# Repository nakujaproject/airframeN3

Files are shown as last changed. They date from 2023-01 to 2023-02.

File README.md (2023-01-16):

# airframeN3

This is the repository for the airframe sub-group relating to N3 rocket.

   

## Onboarding

For new members, please check out onboard document [here](Onboarding/newEmployee.md)

## Research

For visitors, check out our research done by members of the airframe team [here](Research/)

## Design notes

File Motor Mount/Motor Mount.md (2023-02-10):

# **MOTOR MOUNTS**

A mount is required to secure the motor in place during flight. 
Requirements for the motor mount are:

	- It should locate the motor within the skin tube of the airframe.
	- It should handle the forces due to the thrust produced by the motor.

The motor mount is located between the motor and the outer skin of the rocket tube. It's dimensions must,
therefore, be known early on in the design phase for better fitment. Since a solid rocket motor is being used for this
project, the proposed motor mount is to consist of a mounting tube and centering rings/bulkheads for ensuring
concentricity and locating the mounting tube in the airframe tube. 

The inner diameter of the mounting tube is dictated by the outer diameter of the rocket motor. The outer diameter of 
mounting tube determines the inner diameter of the bulkheads. The bulkheads are to be made of aluminum or polycarbonate.
Depending on the desired arrangement we can have two main configurations for the motor mount:

	1. Mounting tube integral with the retaining bulkhead.
		- THe mounting tube and retaining bulkhead are machined from one piece of metal. THe only additional 
		  component required is the locationg ring at the other end of the mounting tube. 
		- This enables for quick locating and assembly of the motor mount.
		- Reduces the number of bulkheads to be used.
		- Machining the mounting tube may be difficult.
	Motor mount configuration 1

	2. Mounting tube separate from bulkheads. 
		- This system used a mounting tube and several bulkheads arranged throughout the length of the motor bay
		  for locating and securign the tube in place.
		- Requires several bulkheads.
		- Longer assembly time.
	Motor mount configuration 2

The decision on the mounting configuration will depend on the size of motor selected i.e. thrust and weight since the
mount is supposed to hold the motor in place on application of full thrust.

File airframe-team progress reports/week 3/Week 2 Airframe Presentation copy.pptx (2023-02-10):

## NAKUJA PROJECT WEEK 2 PRESENTATION

AIRFRAME
1ST FEBRUARY 2023

## Past week’s objectives

Preliminary research on the following listed topics:
- Research on the material to fabricate the airframe.
- Feasibility of Aluminum in fabrication of the airframe.
- Research on the material to be used for fabrication. Settled for Aluminium grade 6061.
- Dual parachute deployment
- Research on launchpad and launch lug designs.

## Design examples

- Fully assembled airframe with nose cone, body tube and tail.

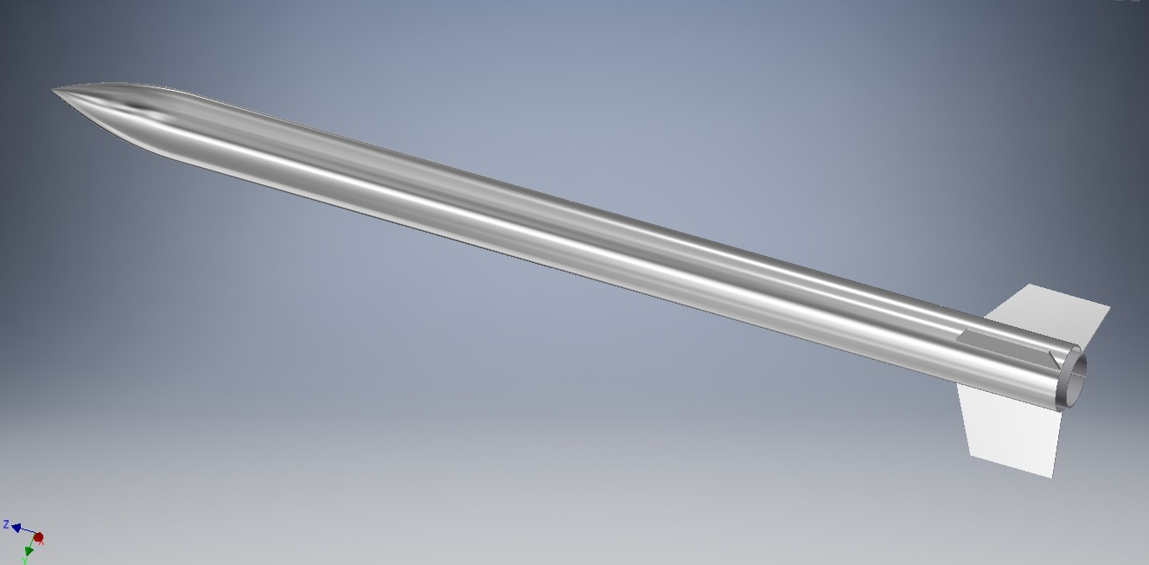
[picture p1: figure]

## Design examples

- Exploded view of the airframe with nose cone, body tube and tail.

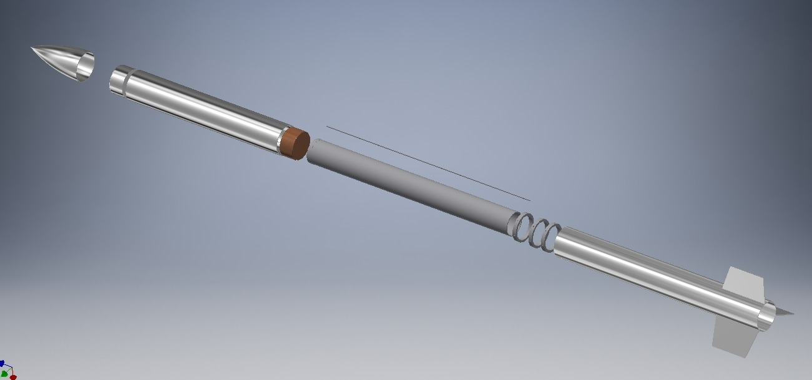
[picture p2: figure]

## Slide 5

- Avionics bay assembly. - Avionics bay inside body tube

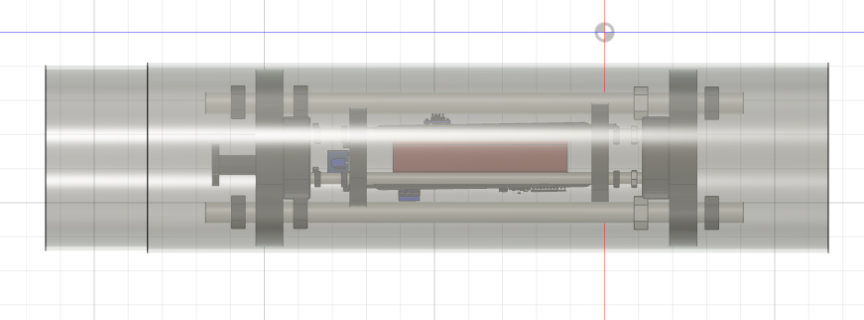
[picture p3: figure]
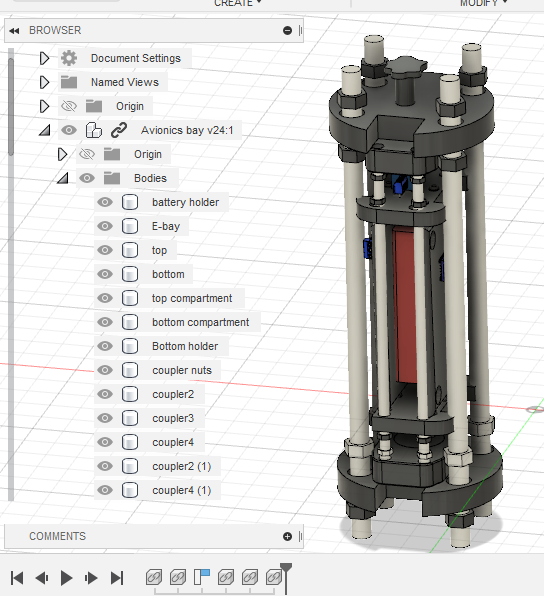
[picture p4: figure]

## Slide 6

- Exploded and assembled view of the motor mount.

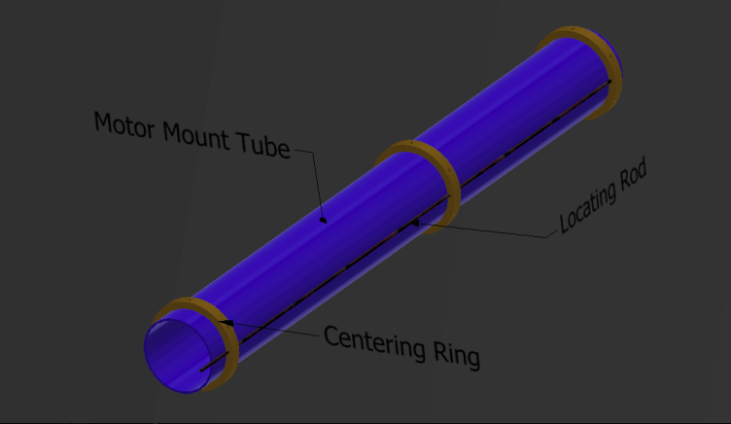
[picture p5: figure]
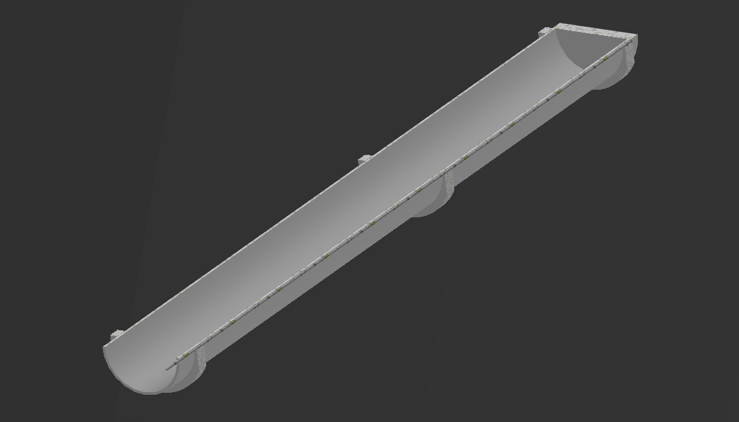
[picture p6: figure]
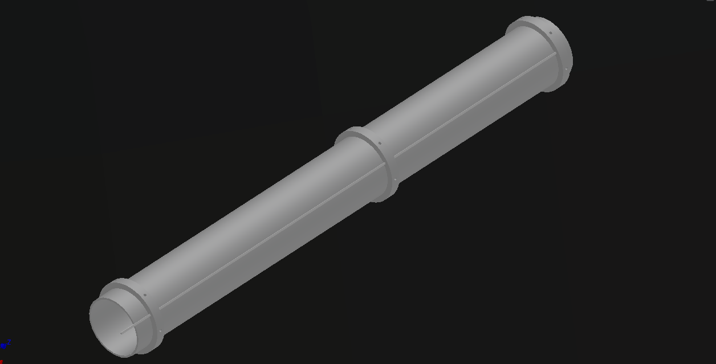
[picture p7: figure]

## Assembled design of the launch pad and launch rod

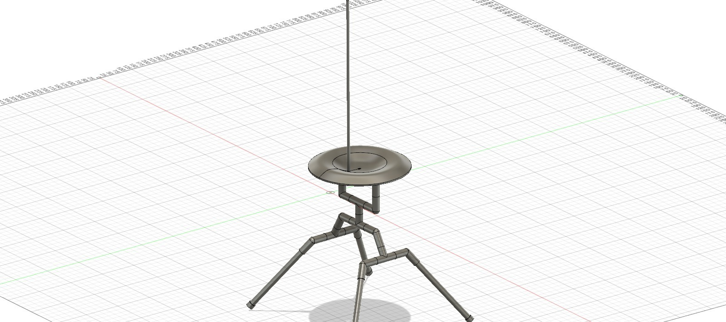
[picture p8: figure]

## Tasklist Spreadsheet

- Link to our Excell tasklist:
https://docs.google.com/spreadsheets/d/1M_BzmsQo8DNNqcfr_GzHXy1NbRIfWbWbaoDP3lDmqlY/edit#gid=1232676584
- Link to Comprehensive Gantt Chart:
Airframe ProjectSchedule (sharepoint.com) (https://studentsjkuatacke-my.sharepoint.com/:x:/r/personal/namuye_innocent_students_jkuat_ac_ke/_layouts/15/Doc.aspx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)
- Link to simplified Gantt Chart:
Simplified Airframe Gantt Chart.xlsx (sharepoint.com) (https://studentsjkuatacke-my.sharepoint.com/:x:/r/personal/namuye_innocent_students_jkuat_ac_ke/_layouts/15/Doc.aspx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)

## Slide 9

- Simplified Airframe Gantt chart

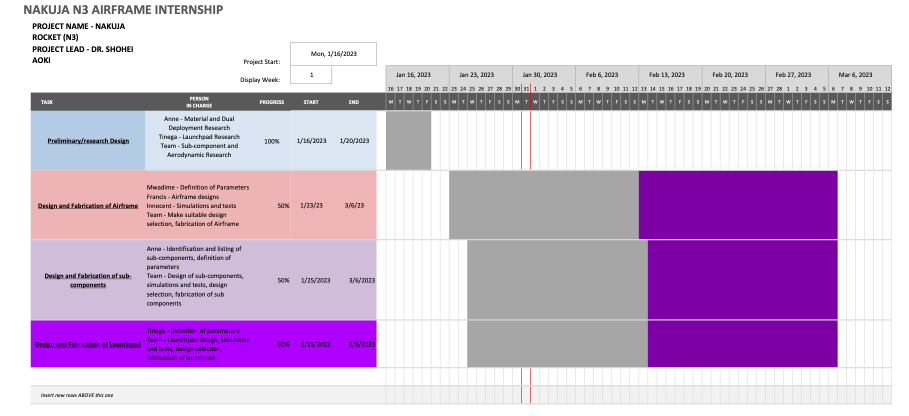
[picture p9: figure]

## Way forward

- Fabricate 5 airframe prototypes
: 3 with fibreglass
; 2 with Aluminium
- One of the fins will be fabricated using carbon fibre
- We are planning to use the aluminum rod instead of sheet for accuracy and ease of fabrication.

## This week’s objectives

- Research and selection of fabrication techniques
- Settle on parameter selection
- Generation of bill of materials
- Finalise on designs
- Make design selection

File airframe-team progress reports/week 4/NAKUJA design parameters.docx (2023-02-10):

Applied Compressive Load

Calculations for the maximum compressive load the rocket can handle given its dimensions are as follows:

Applied Compressive Strength, F_c =(P_(max))/(πDt)

Where, P_(max) is the maximum load on the rocket tube

D is the rocket diameter

t is thickness of the rocket tube

F_c =Compressive strength of aluminium 6061 (120Mpa)

P_(max) =F_c ×π×D×t=120×π×80×2=60,318.578N≅60kN

The actual applied load: (calculated at max Q)

Drag force, F_D =1/2×ρ×C_d ×v^2 ×A

F_D =1/2×1.225×0.64×342^2 ×0.007056=323.52≅325N

Inertia Force, F_(inertia) =ma=10×37=370N

Total applied load=F_D +F_(inertia) =325+370=695N≅700N

The load applied is less than the maximum load the rocket tube can handle. The rocket is thus safe from compression loads during flight.

Maximum Buckling Loads (that the airframe can handle)

Buckling Loads=(γ2πEt^2 cos^2 α)/(√(3(1-μ^2 )))

Where α is the conical semi-angle.

γ=0.33

Buckling loads=(0.33×2π×69×10^9 ×0.003^2 ×cos^2 9.46)/(√(3(1-0.33^2 )))=766.235kN≅770kN

Coefficient of drag on Nose and Body Tube

C_(D_N) +C_(D_(BT)) =1.02C_F (1+1.5/((L/d)^2))(S_(BT))/(A_(BT))

C_(D_N) +C_(D_(BT)) =1.02×2.387×10^(-3) (1+1.5/((186/84)^2))0.40715/0.402124

C_(D_N) +C_(D_(BT)) =2.43474×10^(-3) ×1.3059×1.0125=3.2193×10^(-3)

Base Drag Coefficient

C_(D_B) =0.029/(√(C_(D_N) +C_(D_(BT))))=0.029/(√(3.2193×10^(-3)))=0.51112

Fin Drag Coefficient

C_(D_F) =2C_F (1+2t/(C_(ave)))(S_F)/(A_(BT))=2×2.387^(-3) (1+20.003/0.115)0.0095/0.402124=1.1867×10^(-4)

Intermediate Drag Coefficient

C_(D_I) =C_F (1+2t/(C_(ave)))(C_R)/(S_(BT))∙dn=2.387×10^(-3) (1+20.003/0.115)0.08/0.40715∙0.08×3

C_(D_I) =1.18437×10^(-4)

Total Drag Coefficient

C_D =C_(D_N) +C_(D_(BT)) +C_(D_B) +C_(D_F) +C_(D_I) =3.2193×10^(-3) +0.51112+1.1867×10^(-4) +1.18437×10^(-4) ≅0.5146

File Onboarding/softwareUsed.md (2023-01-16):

# Used software

## Initial Design

Currently we are using [Openrocket v22.02](https://openrocket.info/downloads.html?vers=22.02.beta.05)

## Computer Aided Design

Currently we are using [Inventor 2022](https://knowledge.autodesk.com/support/inventor/learn-explore/caas/CloudHelp/cloudhelp/2020/ENU/Inventor-WhatsNew/files/GUID-8126E8EE-422A-4DEF-9B14-513D87BD4122-htm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's,the%20release%20of%20Inventor%202020.&text=Inventor%202020%20delivers%3A,a%20modernized%20look%20and%20feel.)

## Analysis

For fluid analysis we are using [CFD 2022](https://knowledge.autodesk.com/support/cfd/troubleshooting/caas/downloads/content/autodesk-cfd-2019-download-and-install-help-documentation.html)

The Autodesk fusion version we are using is [Fusion 360](https://www.autodesk.com/products/fusion-360/free-trial)

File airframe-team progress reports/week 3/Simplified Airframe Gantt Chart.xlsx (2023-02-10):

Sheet: About
SIMPLE GANTT CHART by Vertex42.com (https://www.vertex42.com/ExcelTemplates/simple-gantt-chart.html)
https://www.vertex42.com/ExcelTemplates/simple-gantt-chart.html
About This Template
This template provides a simple way to create a Gantt chart to help visualize and track your project. Simply enter your tasks and start and end dates - no formulas required. The bars in the Gantt chart represent the duration of the task and are displayed using conditional formatting. Insert new tasks by inserting new rows.
Guide for Screen Readers
There are 2 worksheets in this workbook. TimeSheet About The instructions for each worksheet are in the A column starting in cell A1 of each worksheet. They are written with hidden text. Each step guides you through the information in that row. Each subsequent step continues in cell A2, A3, and so on, unless otherwise explicitly directed. For example, instruction text might say "continue to cell A6" for the next step. This hidden text will not print. To remove these instructions from the worksheet, simply delete column A.
Additional Help
Click on the link below to visit vertex42.com and learn more about how to use this template, such as how to calculate days and work days, create task dependencies, change the colors of the bars, add a scroll bar to make it easier to change the display week, extend the date range displayed in the chart, etc.
How to Use the Simple Gantt Chart (https://www.vertex42.com/ExcelTemplates/simple-gantt-chart.html)
More Project Management Templates
Visit Vertex42.com to download other project management templates, including different types of project schedules, Gantt charts, tasks lists, etc.
Project Management Templates (https://www.vertex42.com/ExcelTemplates/excel-project-management.html)
About Vertex42
Vertex42.com provides over 300 professionally designed spreadsheet templates for business, home, and education - most of which are free to download. Their collection includes a variety of calendars, planners, and schedules as well as personal finance spreadsheets for budgeting, debt reduction, and loan amortization.
Businesses will find invoices, time sheets, inventory trackers, financial statements, and project planning templates. Teachers and students will find resources such as class schedules, grade books, and attendance sheets. Organize your family life with meal planners, checklists, and exercise logs. Each template is thoroughly researched, refined, and improved over time through feedback from thousands of users.

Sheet: ProjectSchedule
NAKUJA N3 AIRFRAME INTERNSHIP
Enter Company Name in cell B2. | PROJECT NAME - NAKUJA ROCKET (N3)
Enter the name of the Project Lead in cell B3. Enter the Project Start date in cell E3. Project Start: label is in cell C3. | PROJECT LEAD - DR. SHOHEI AOKI | Project Start: |  | 2023-01-16
The Display Week in cell E4 represents the starting week to display in the project schedule in cell I4. The project start date is considered Week 1. To change the display week, simply enter a new week number in cell E4. The starting date for each week, starting with the display week from cell E4, starts in cell I4 and is auto calculated. There are 8 weeks represented in this view from cell I4 through cell BF4. You should not modify these cells. Display Week: label is in cell C4. |  | Display Week: |  | 1 |  | 2023-01-16 |  |  |  |  |  |  | 2023-01-23 |  |  |  |  |  |  | 2023-01-30 |  |  |  |  |  |  | 2023-02-06 |  |  |  |  |  |  | 2023-02-13 |  |  |  |  |  |  | 2023-02-20 |  |  |  |  |  |  | 2023-02-27 |  |  |  |  |  |  | 2023-03-06
Cells I5 through BL5 contain the day number for the week represented in the cell block above each date cell and are auto calculated. You should not modify these cells. Today's date is outlined in Red (hex #AD3815) from today's date in row 5 through the entire date column to the end of the project schedule. |  |  |  |  |  | 2023-01-16 | 2023-01-17 | 2023-01-18 | 2023-01-19 | 2023-01-20 | 2023-01-21 | 2023-01-22 | 2023-01-23 | 2023-01-24 | 2023-01-25 | 2023-01-26 | 2023-01-27 | 2023-01-28 | 2023-01-29 | 2023-01-30 | 2023-01-31 | 2023-02-01 | 2023-02-02 | 2023-02-03 | 2023-02-04 | 2023-02-05 | 2023-02-06 | 2023-02-07 | 2023-02-08 | 2023-02-09 | 2023-02-10 | 2023-02-11 | 2023-02-12 | 2023-02-13 | 2023-02-14 | 2023-02-15 | 2023-02-16 | 2023-02-17 | 2023-02-18 | 2023-02-19 | 2023-02-20 | 2023-02-21 | 2023-02-22 | 2023-02-23 | 2023-02-24 | 2023-02-25 | 2023-02-26 | 2023-02-27 | 2023-02-28 | 2023-03-01 | 2023-03-02 | 2023-03-03 | 2023-03-04 | 2023-03-05 | 2023-03-06 | 2023-03-07 | 2023-03-08
This row contains headers for the project schedule that follows below them. Navigate from B6 through BL 6 to hear the content. The first letter of each day of the week for the date above that heading, starts in cell I6 and continues through cell BL6. All project timeline charting is auto generated based on the start and end dates entered, using conditional formats. Do not modify content in cells within columns after column I starting with cell I7. | TASK | PERSON IN CHARGE | PROGRESS | START | END | M | T | W | T | F | S | S | M | T | W | T | F | S | S | M | T | W | T | F | S | S | M | T | W | T | F | S | S | M | T | W | T | F | S | S | M | T | W | T | F | S | S | M | T | W | T | F | S | S | M | T | W
Cell B8 contains the Phase 1 sample title. Enter a new Title in cell B8. Enter a name to assign the phase to, if it applies for your project, in cell C8. Enter Progress for the entire phase, if it applies for your project, in cell D8. Enter the start and end dates for the entire phase, if it applies for your project, in cells E8 and F8. The Gantt chart will automatically fill in the appropriate dates and shade according to the progress entered. To delete the phase and work only from tasks, simply delete this row. | Preliminary/research Design | Anne - Material and Dual Deployment Research Tinega - Launchpad Research Team - Sub-component and Aerodynamic Research | 100% | 2023-01-16 | 2023-01-20
The cell at right contains the Phase 2 sample title. You can create a new phase at any time within column B. This project schedule does not require phases. To remove the phase, simply delete the row. To create a new phase block in this row, enter a new Title in cell at right. To continue adding tasks to the phase above, enter a new row above this one and fill in the task data as in cell A9's instruction. Update the Phase details in cell at right based on cell A8's instruction. Continue navigating down column A cells to learn more. If you haven't added any new rows in this worksheet, you will find 2 additional sample phase blocks have been created for you in cells B20 and B26. Otherwise, navigate through column A cells to find the additional blocks. Repeat the instructions from cells A8 and A9 whenever you need to. | Design and Fabrication of Airframe | Mwadime - Definition of Parameters Francis - Airframe designs Innocent - Simulations and tests Team - Make suitable design selection, fabrication of Airframe | 50% | 2023-01-23 | 2023-03-06
Sample phase title block | Design and Fabrication of sub-components | Anne - Identification and listing of sub-components, definition of parameters Team - Design of sub-components, simulations and tests, design selection, fabrication of sub components | 50% | 2023-01-25 | 2023-03-06
 | Design and Fabrication of Launchpad | Tinega - Definition of parameters Team - Launchpad design, simulation and tests, design selection, fabrication of launchpad | 50% | 2023-01-25 | 2023-03-06
This is an empty row
This row marks the end of the Project Schedule. DO NOT enter anything in this row. Insert new rows ABOVE this one to continue building out your Project Schedule. | Insert new rows ABOVE this one
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

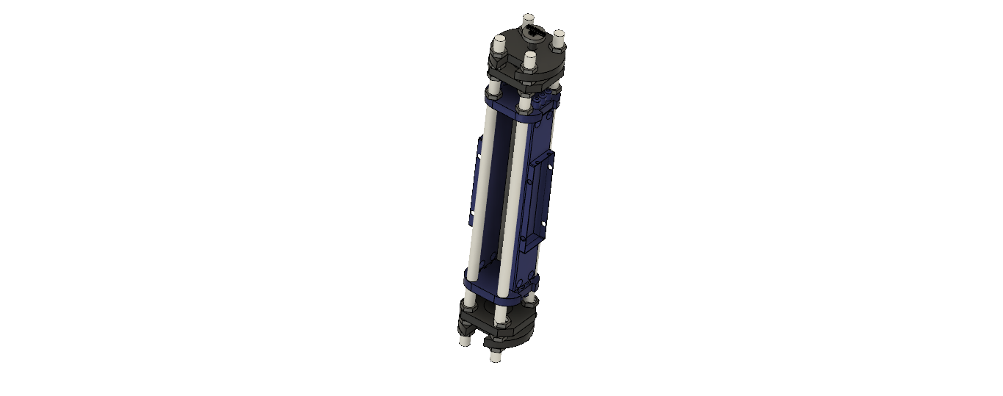
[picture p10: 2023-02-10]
airframe-team progress reports/week 4/Airframe Design Images/N3 avionics bay.png

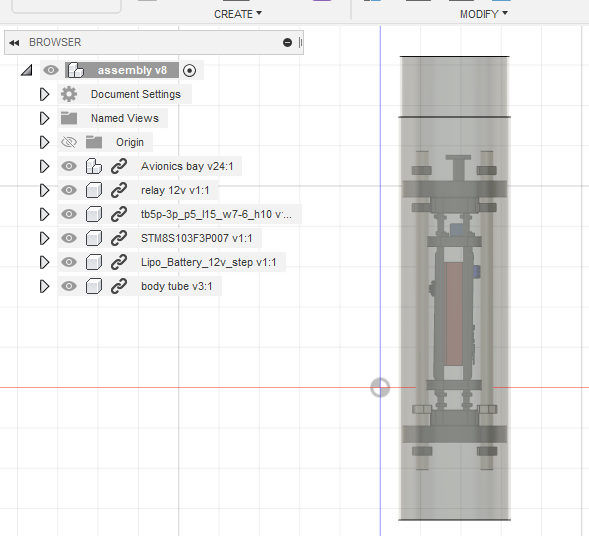
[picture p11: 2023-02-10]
airframe-team progress reports/week 3/Avionics bayV1/vionics .png

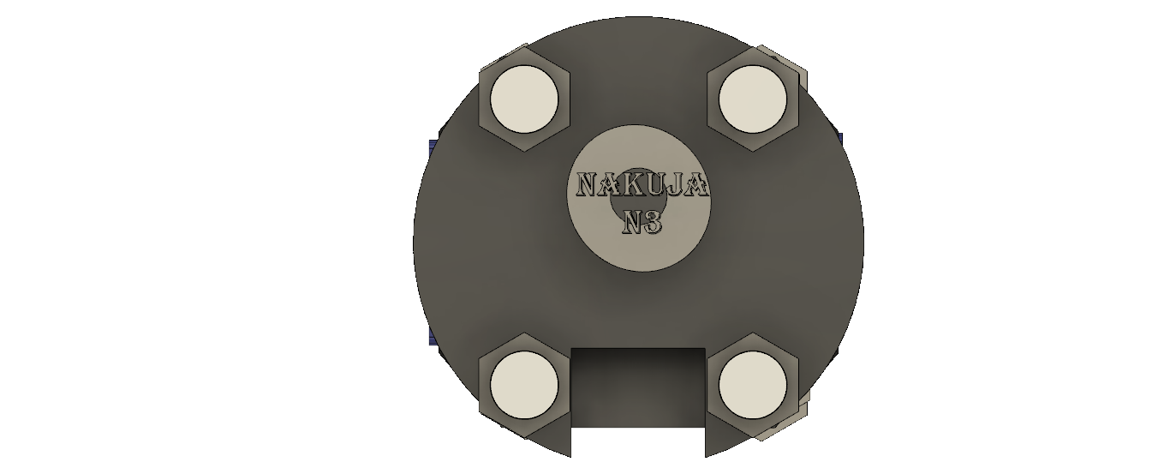
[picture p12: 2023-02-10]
airframe-team progress reports/week 4/Airframe Design Images/Top view.png

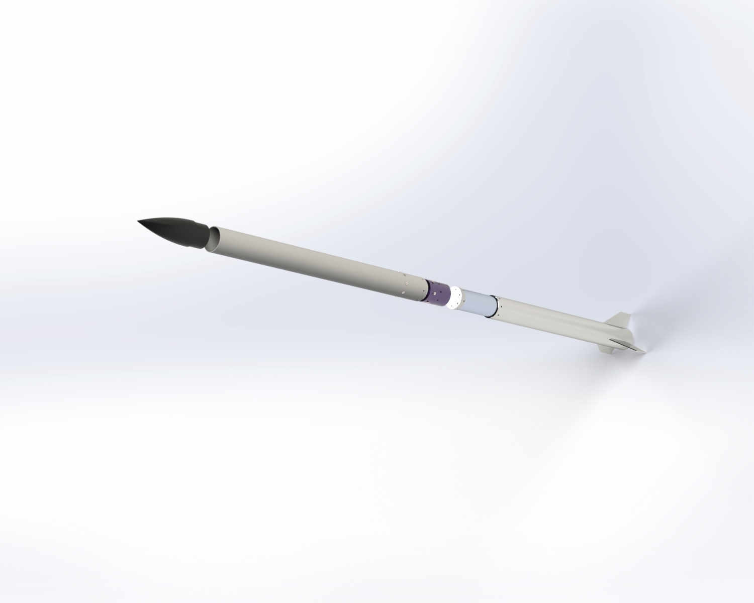
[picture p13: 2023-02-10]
airframe-team progress reports/week 4/Airframe Design Images/Rendered View.jpeg

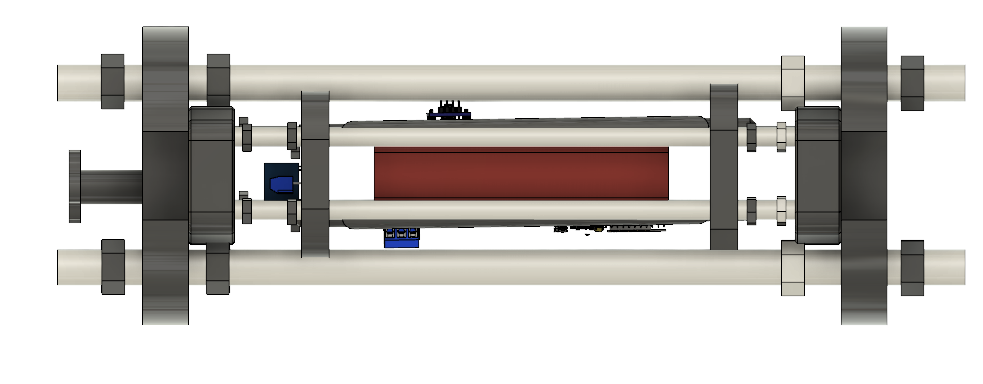
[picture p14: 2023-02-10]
airframe-team progress reports/week 3/Avionics bayV1/frontview.png

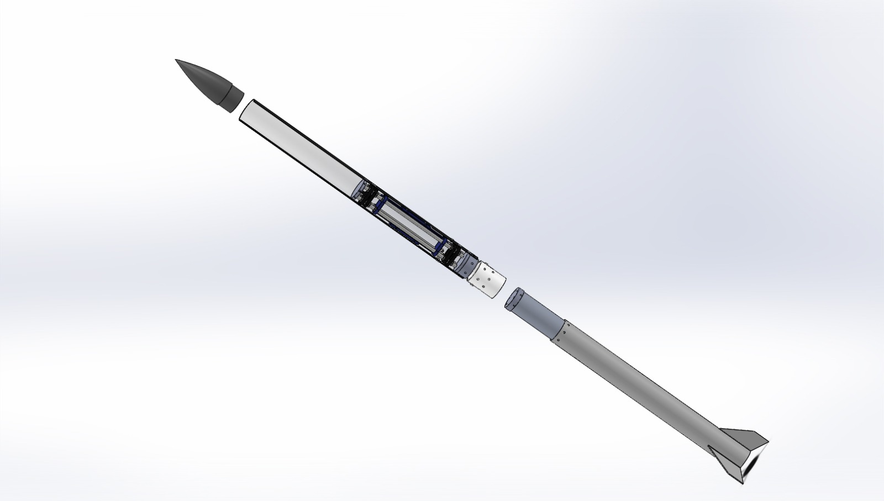
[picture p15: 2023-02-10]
airframe-team progress reports/week 4/Airframe Design Images/Exploaded view.jpeg

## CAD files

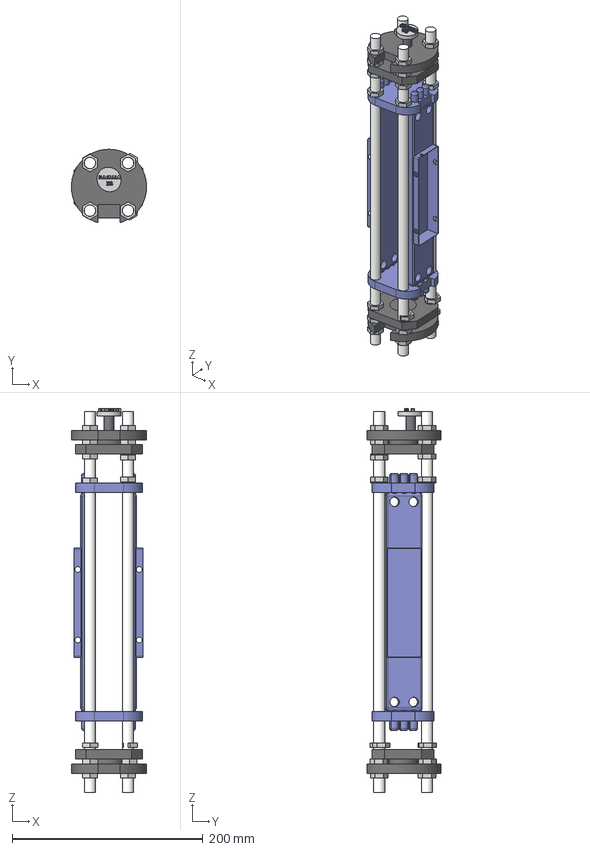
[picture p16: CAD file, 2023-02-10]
airframe-team progress reports/week 4/CAD files/Final assemblyv2 v9.step
79.0 x 77.3 x 403.0 mm
Holder Avionics Bay
holder_rod x 4
Holder Avionics Bay v5(Mirror)
bottom compartment
Bottom coupler
bottom compartment v11(Mirror)
Bottom coupler v4(Mirror)
Ebay x 2
Holder
holder_nut x 28

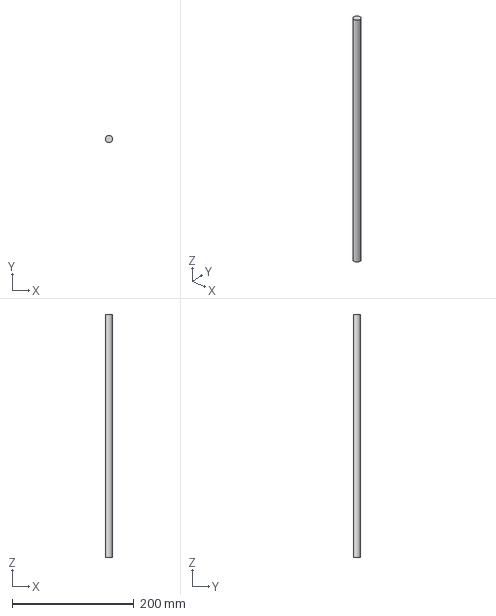
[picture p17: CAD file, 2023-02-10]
airframe-team progress reports/week 4/CAD files/N3 holder_rod .step
11.8 x 11.8 x 400.0 mm

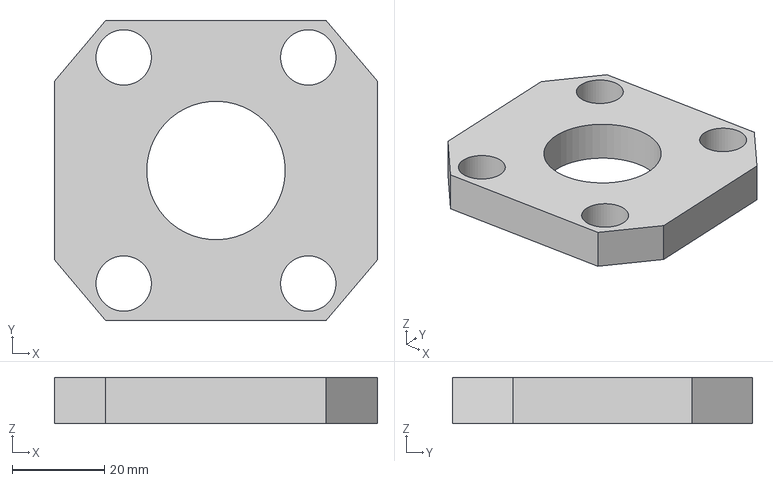
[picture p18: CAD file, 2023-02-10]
airframe-team progress reports/week 4/CAD files/N3 bottom compartment .step
70.0 x 65.0 x 10.0 mm

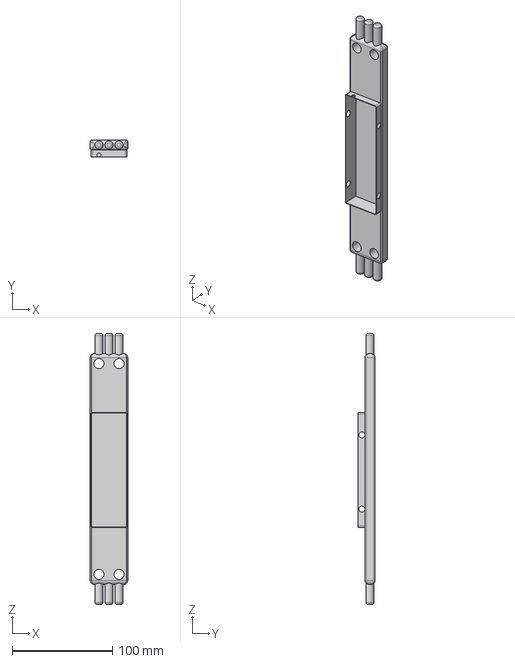
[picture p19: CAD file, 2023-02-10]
airframe-team progress reports/week 4/CAD files/N3 Ebay .step
37.5 x 17.0 x 270.0 mm

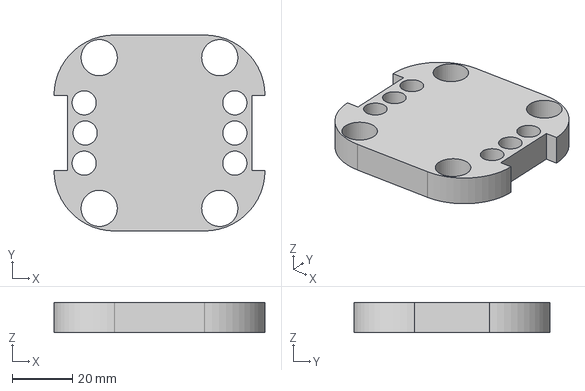
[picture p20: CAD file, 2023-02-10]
airframe-team progress reports/week 4/CAD files/N3 Bottom coupler.step
70.0 x 65.0 x 10.0 mm

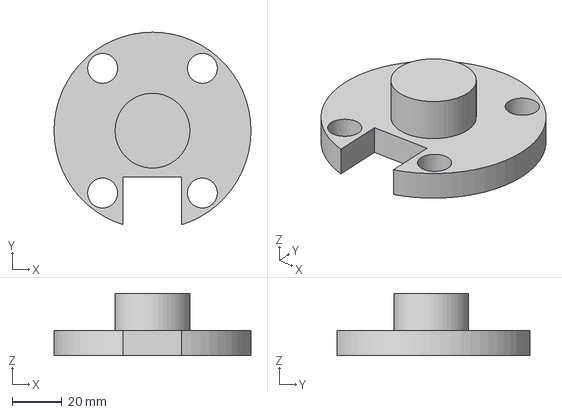
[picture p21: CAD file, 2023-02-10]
airframe-team progress reports/week 4/CAD files/N3 Holder Avionics Bay.step
79.0 x 77.3 x 25.0 mm

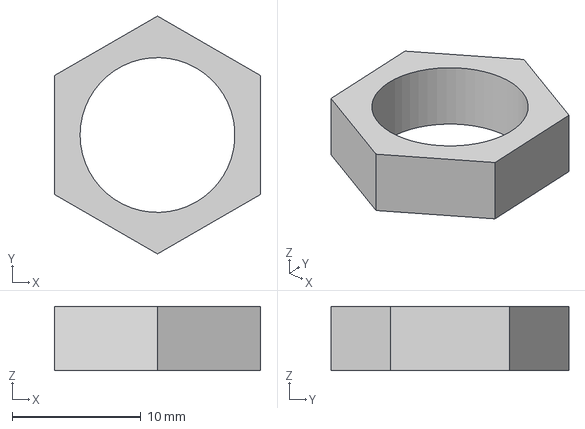
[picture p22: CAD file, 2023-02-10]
airframe-team progress reports/week 4/CAD files/N3 holder_nut .step
16.0 x 18.5 x 5.00 mm

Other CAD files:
airframe-team progress reports/week 4/CAD files/N3 Avionics bay.step

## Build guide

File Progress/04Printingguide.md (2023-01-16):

# 3D prinitng basics on `ULTIMAKER s3`

## Theory

This is from the ultimaker site.

### Layer height

It is the thickness of one printed layer in millimeters.
Thinner layer height increases the quality of the print, leading to a smoother surface and more detail model.

### Initial layer height

This is the height of the first layer of your print. The initial layer height is usually thicker than the layer height to create a stronger adhesion with the build plate.

### Line width

The width of a single printed line, which should be close to the nozzle size.

- Top surface skin line width: This line width is only available when a top surface skin is used.
- Top/bottom line width: The line width with which the top and bottom layers are printed.
- Infill line width: The line width of all infill material.

### Infill density

It is the amount of plastic used on the inside of the print. A higher infill density means that there is more plastic on the inside of your print, leading to a stronger object.

### Infill pattern

This is the pattern of the infill material.

- Strong 2D infills are used for everyday prints
- Quick 2D infills are used for quick, but weak models
- 3D infills are used to make the object equally strong in all directions
- 3D concentric infills are used for flexible materials

The following pattern options are available:

- Grid: Strong 2D infill
- Lines: Quick 2D infill
- Triangles: Strong 2D infill
- Tri-hexagon: Strong 2D infill
- Cubic: Strong 3D infill
- Cubic (subdivision): Strong 3D infill (this saves material compared to Cubic)
- Octet: Strong 3D infill
- Quarter cubic: Strong 3D infill
- Concentric: Flexible 3D infill
- Zig-zag: A grid shaped infill, printing continuously in one diagonal direction
- Cross: Flexible 3D infill
- Cross 3D: Flexible 3D infill
- Gyroid infill: Infill with increased strength for the lowest weight.

### Printing temperature

The temperature of the nozzle while printing, including the adapted extrusion rate. Each printing profile has a slightly different printing temperature to create the best print result.

### Build plate temperature

The heated bed temperature during the printing process. Each material has an ideal build plate temperature, which is set here.

### Print speed

The print speed defines the speed (in mm/s) at which the print head moves while printing. Based on this setting, Ultimaker Cura calculates the extrusion flow.

A higher print speed will lead to a shorter print time. Keep in mind that increasing the print speed means that you may have to increase the temperature as well to ensure the filament is properly melted.

### Enable cooling fans

With this setting you can enable or disable the print head fans during printing. The print head fans ensure that the material is cooled properly before the next layer is printed. For layers with a short layer time, and those with bridges/overhangs, cooling will increase the print quality.

### Fan speed

When the print head fans are enabled, you can adjust certain parameters. One of these is the fan speed – the speed at which the fans spin. A higher speed allows for better cooling and reduces oozing, but can also increase the shrinkage of the material.

### Build plate adhesion

#### Raft

A raft adds a thick grid with a roof between the model and the build plate. This can be useful when the bottom surface of a model is not completely flat or has little adhesion to the build plate. A raft ensures that the model will stick better to the build plate.

#### Brim

Brim adds a single layer flat area around the base of the model to prevent warping. The brim is connected to the model and makes the bottom surface area bigger. This increases the adhesion to the build plate and, in case of warping, the corners of the model are less likely to curl up because of the brim attached to it.

## Process

### 1. Open your model to import it inside ultimaker cura software

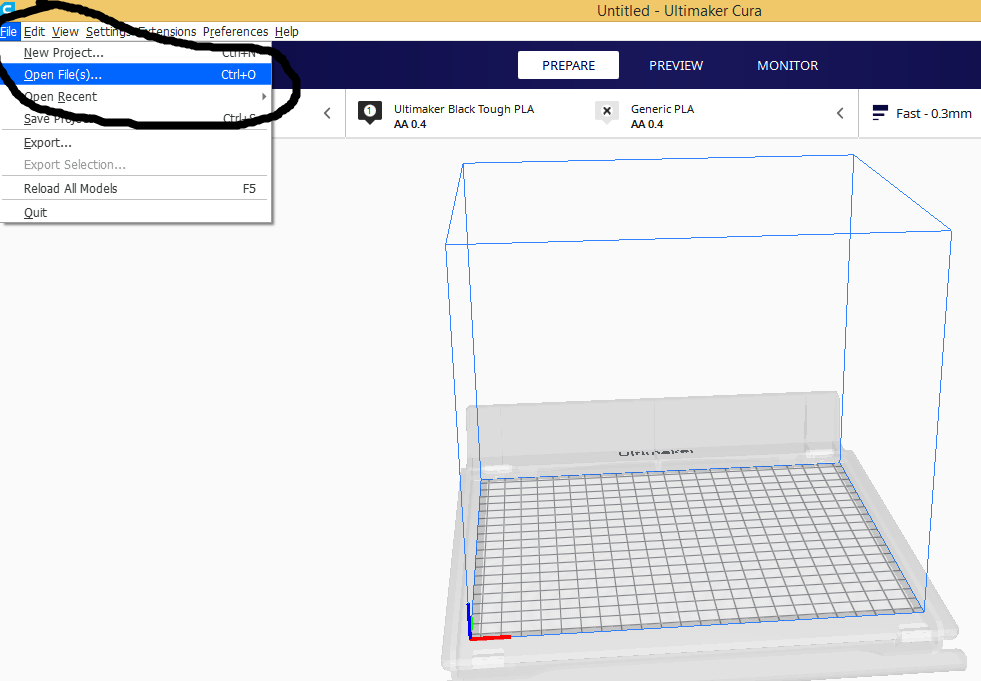
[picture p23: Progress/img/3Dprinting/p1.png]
[](img/3Dprinting/p1.png)

### 2. The model has been imported with the orientation in which you drew it

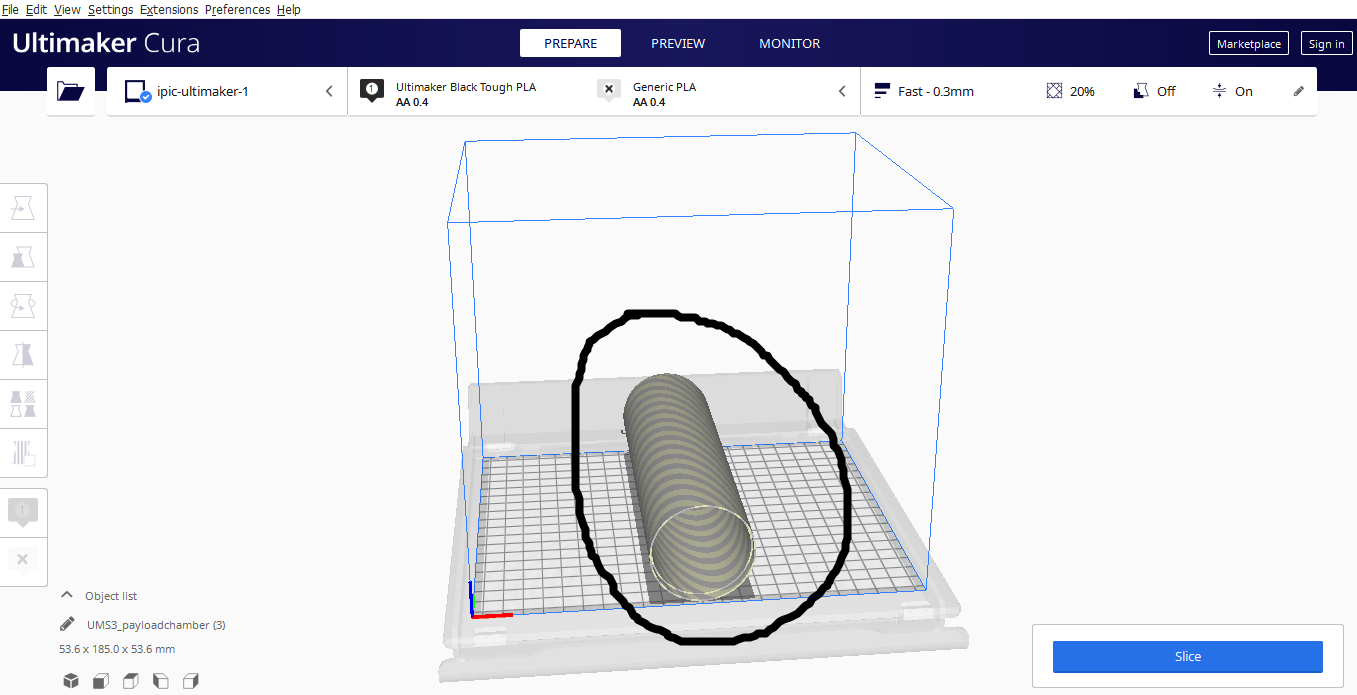
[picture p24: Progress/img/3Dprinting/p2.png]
[](img/3Dprinting/p2.png)

### 3. Change the orientation so that it lies vertically

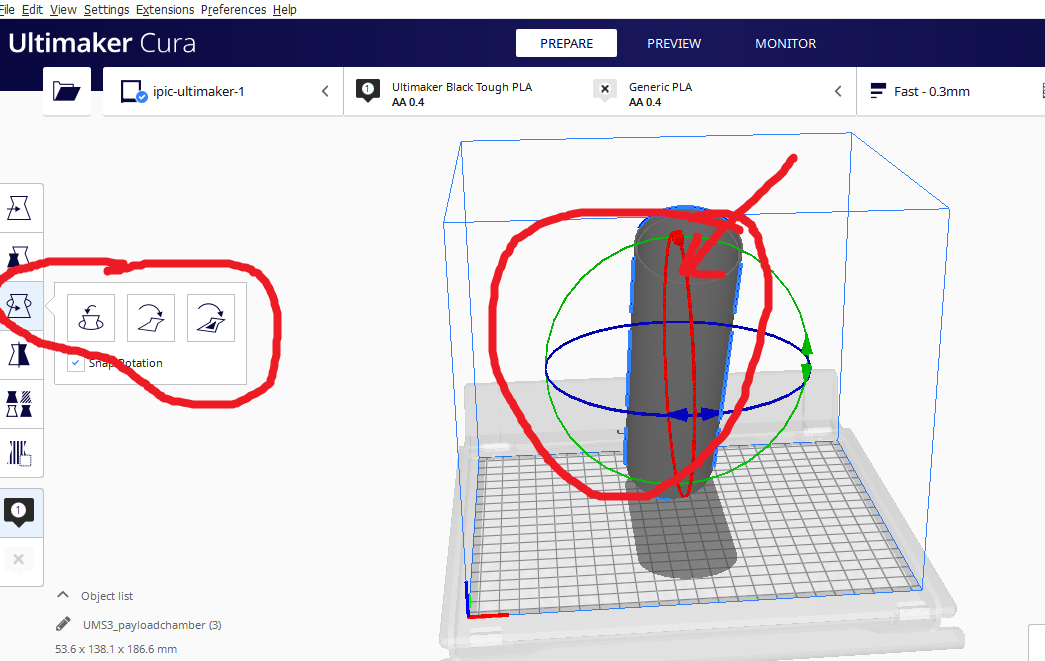
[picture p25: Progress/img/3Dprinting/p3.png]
[](img/3Dprinting/p3.png)

### 4. Click on the lay flat so that it can automatically set the base to the bed

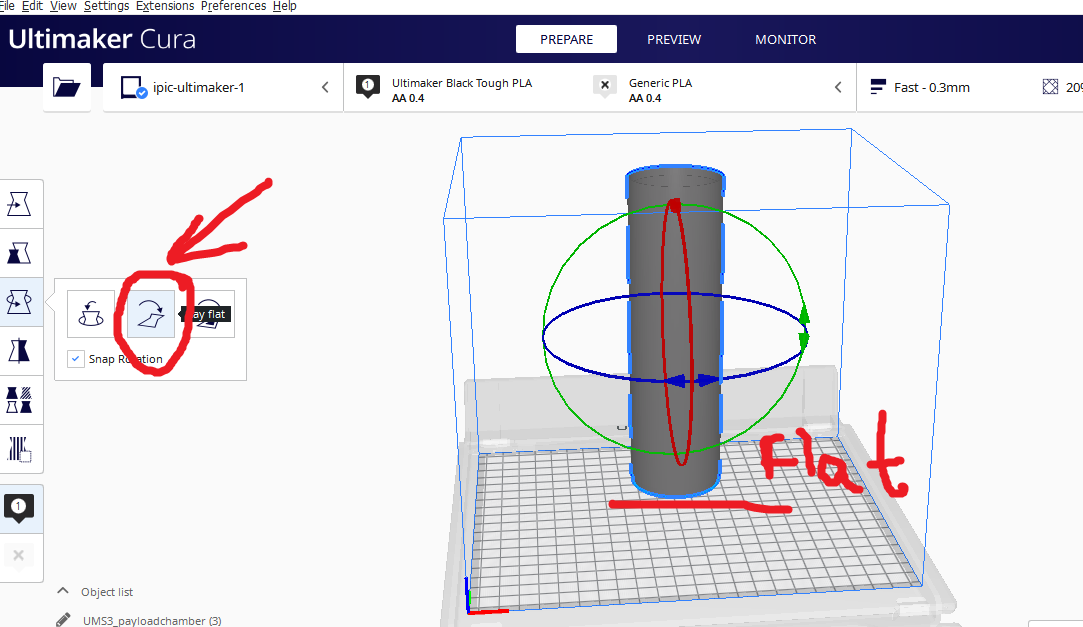
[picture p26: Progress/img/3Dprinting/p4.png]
[](img/3Dprinting/p4.png)

### 5. Center the model on the bed

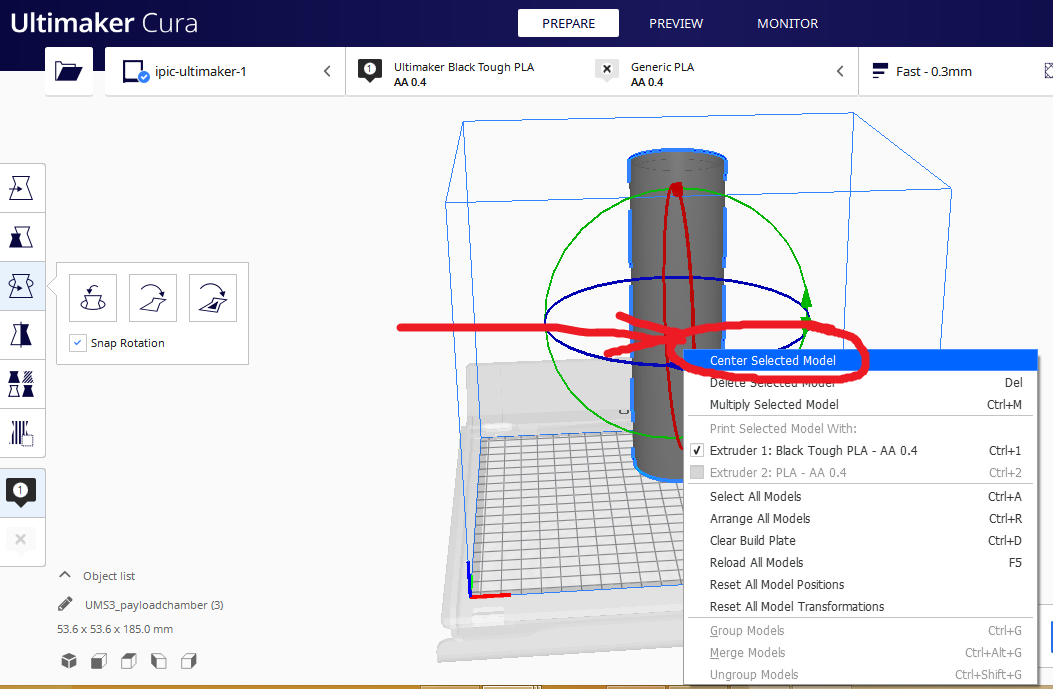
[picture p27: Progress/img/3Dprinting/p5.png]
[](img/3Dprinting/p5.png)

### 6. You can scale down the model with the height alone. Click to remove uniform scaling in order to scal e the height alone

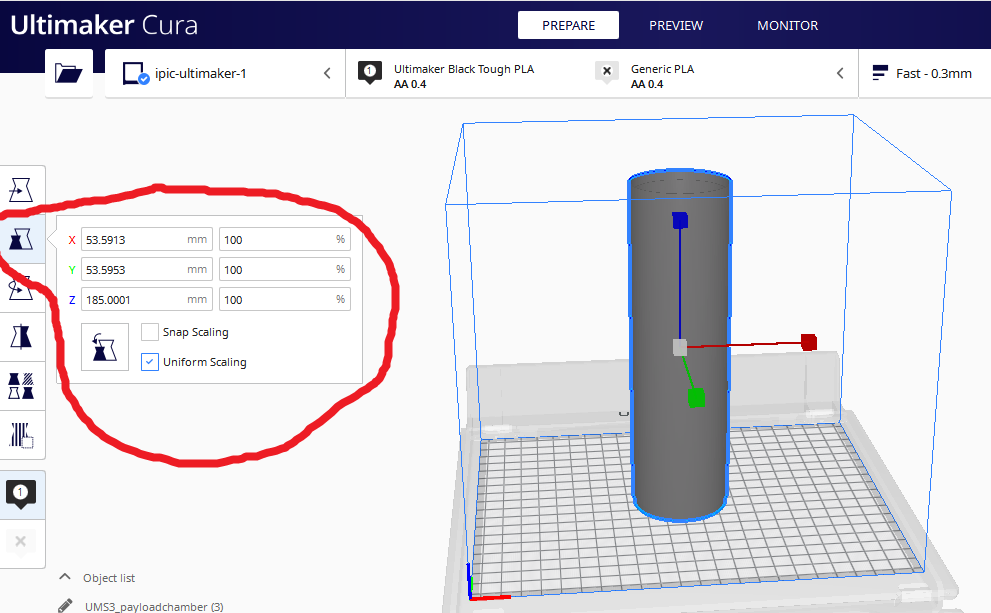
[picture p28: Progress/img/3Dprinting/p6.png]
[](img/3Dprinting/p6.png)

### 7. The model has been scaled down in terms of height

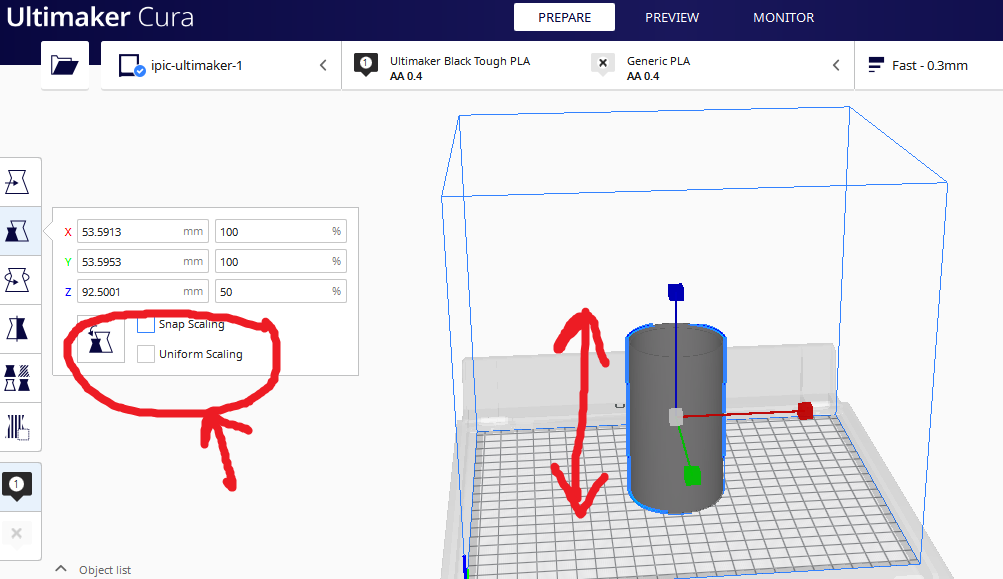
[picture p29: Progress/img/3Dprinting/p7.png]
[](img/3Dprinting/p7.png)

### 8. Click on the top right conrer in order to change the print settings

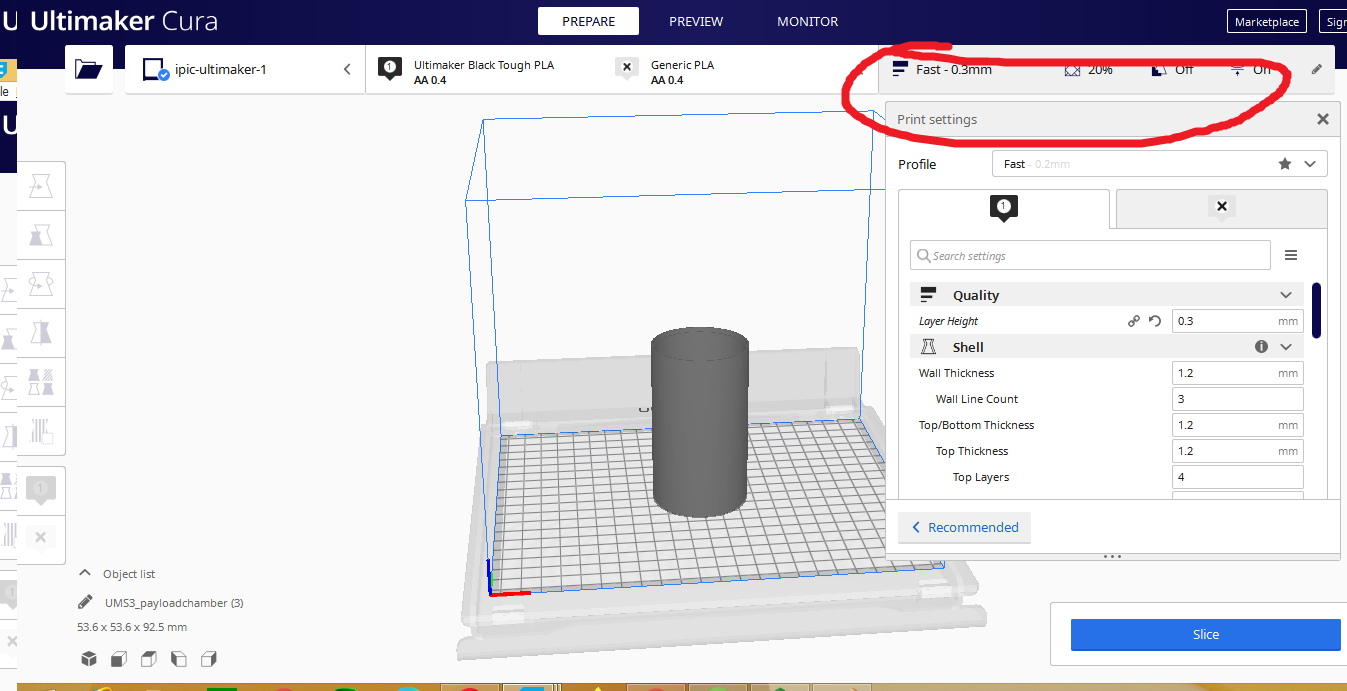
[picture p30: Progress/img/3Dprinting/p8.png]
[](img/3Dprinting/p8.png)

### 9. Change it to normal

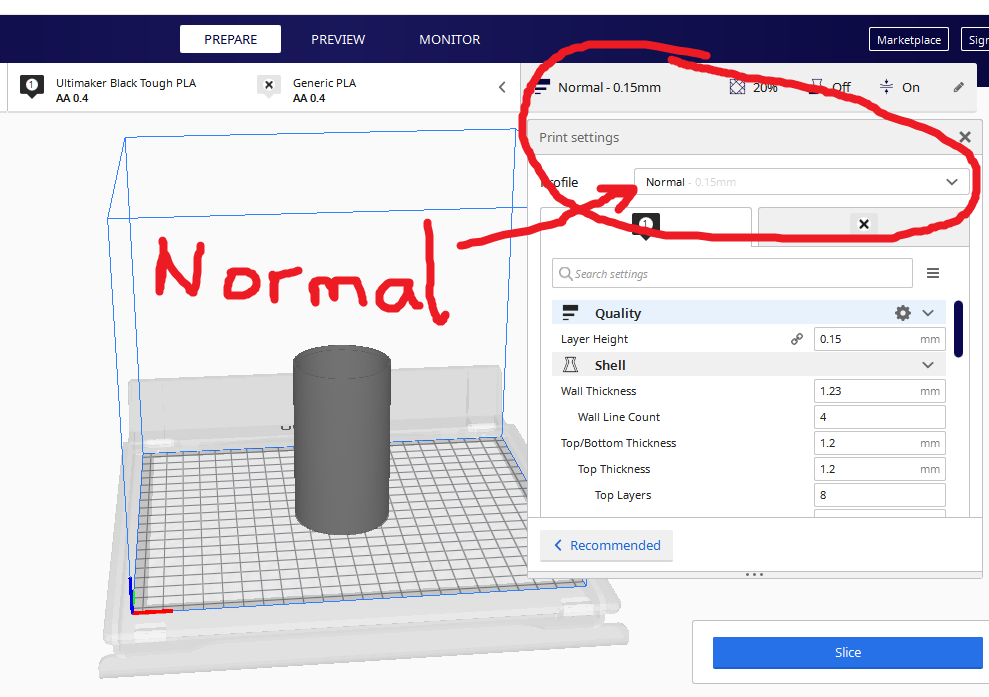
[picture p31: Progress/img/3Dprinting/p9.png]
[](img/3Dprinting/p9.png)

### 10. Change the layer height to 0.2mm

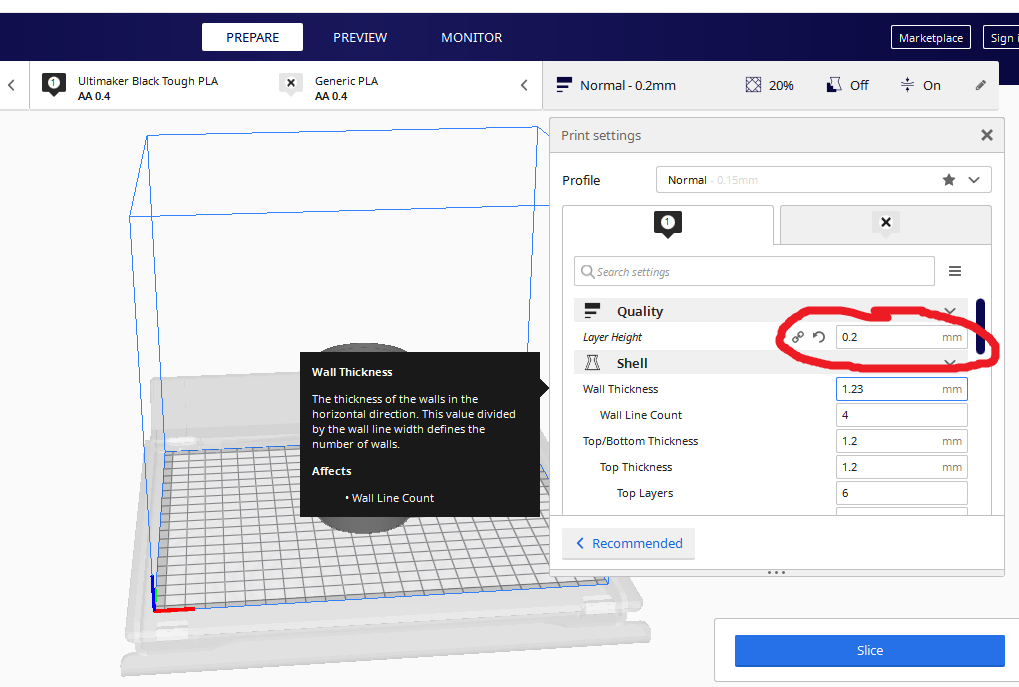
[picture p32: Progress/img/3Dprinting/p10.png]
[](img/3Dprinting/p10.png)

### 11. Maintain the top and bottom thickness to 1.2mm with 6 layers

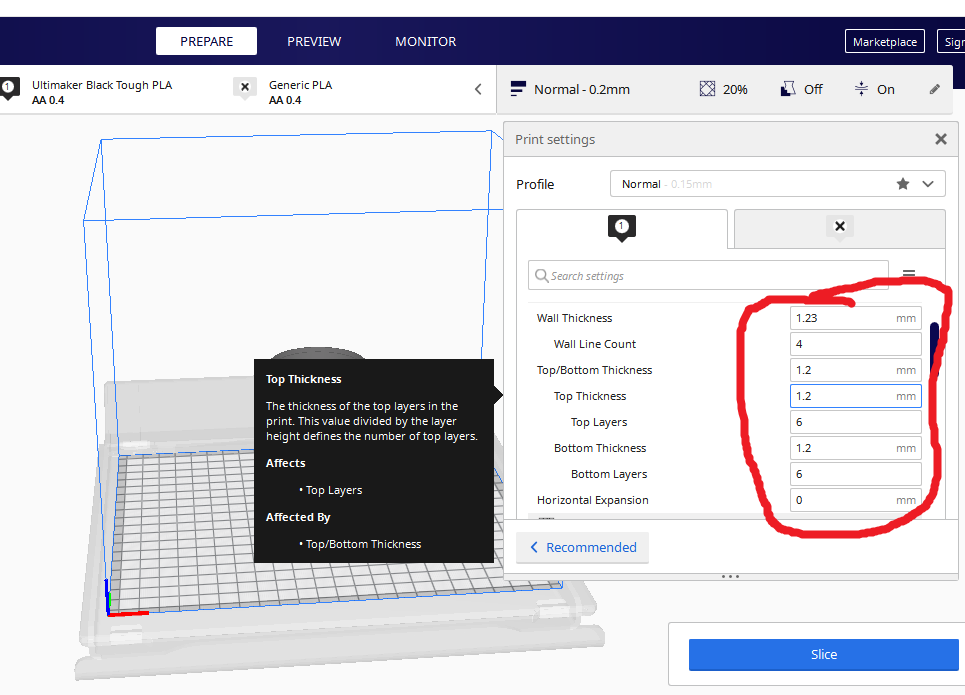
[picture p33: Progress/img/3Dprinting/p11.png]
[](img/3Dprinting/p11.png)

### 12. Change the infill pattern to `Lines` also the temperature set the printing temperature to `223 C` and build plate temperature to `70 C`

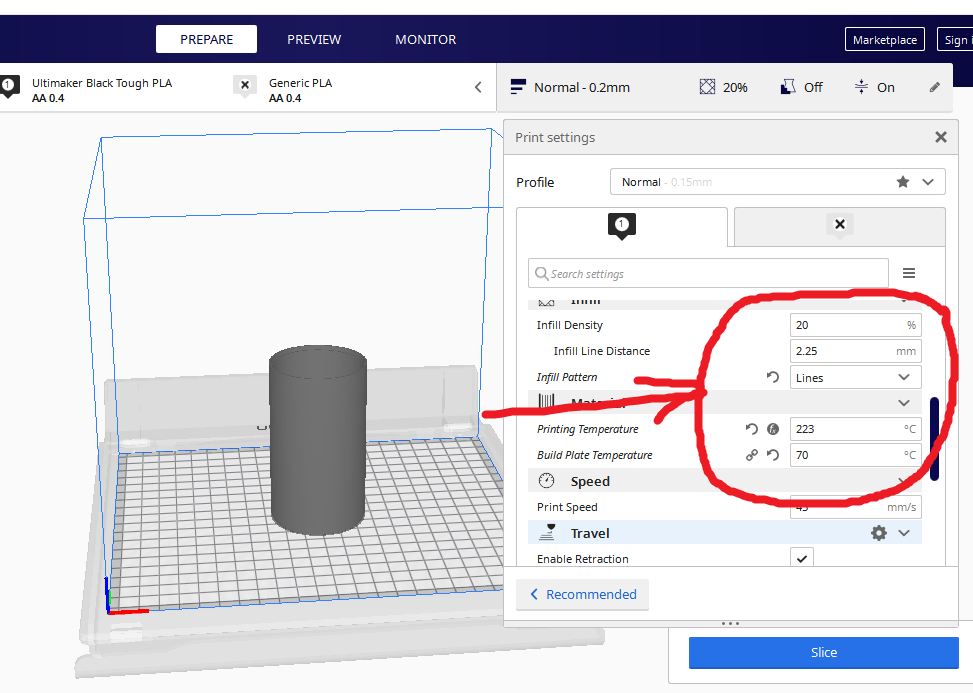
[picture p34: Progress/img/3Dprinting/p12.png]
[](img/3Dprinting/p12.png)

### 13. Enable print cooling at 100%

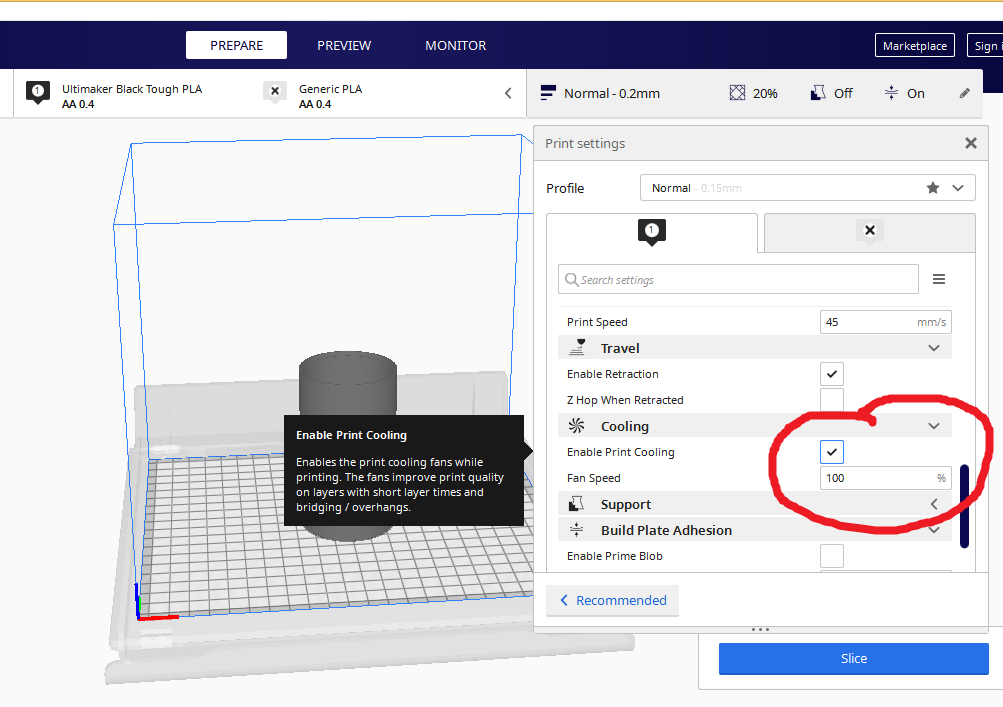
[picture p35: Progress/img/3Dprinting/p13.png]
[](img/3Dprinting/p13.png)

### 14. Change the build plate adhesion type to `Raft` with a margin of `5mm`

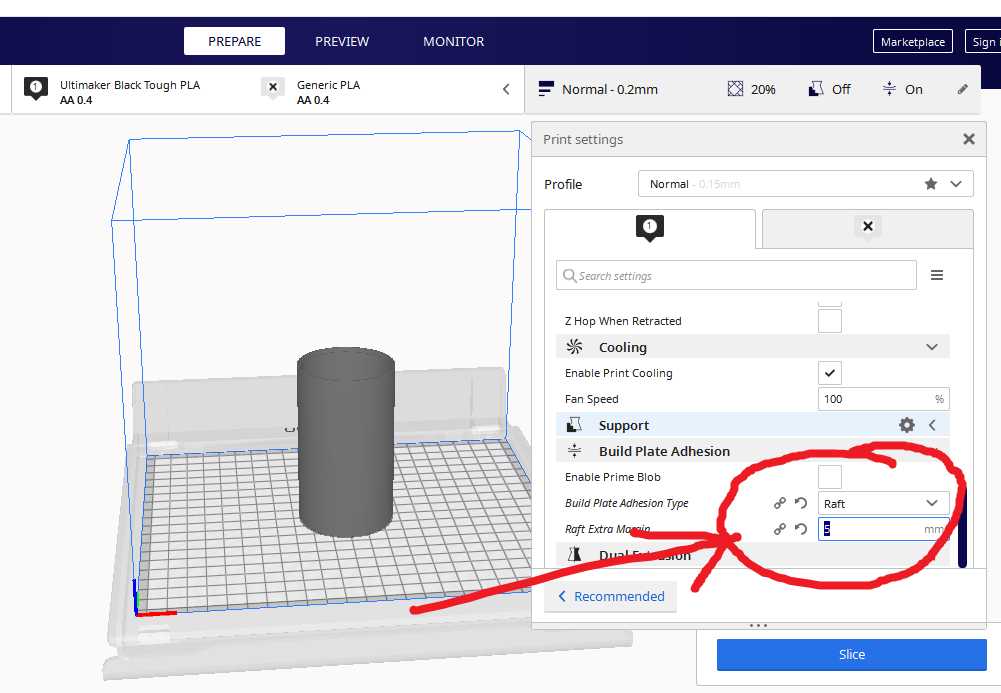
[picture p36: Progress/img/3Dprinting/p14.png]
[](img/3Dprinting/p14.png)

### 16. Click on the machine you want to print. This is for machines connected in the network and print

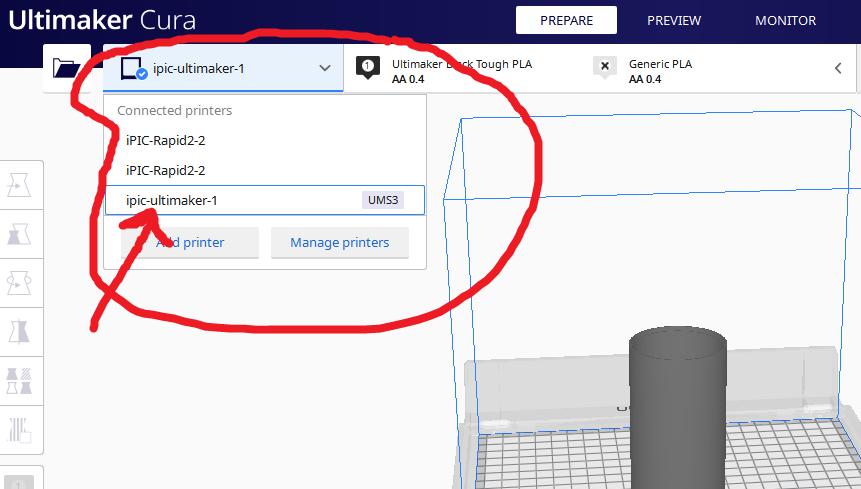
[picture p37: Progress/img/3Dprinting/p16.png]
[](img/3Dprinting/p16.png)

### 17. Monitor the prinitng process using a camera

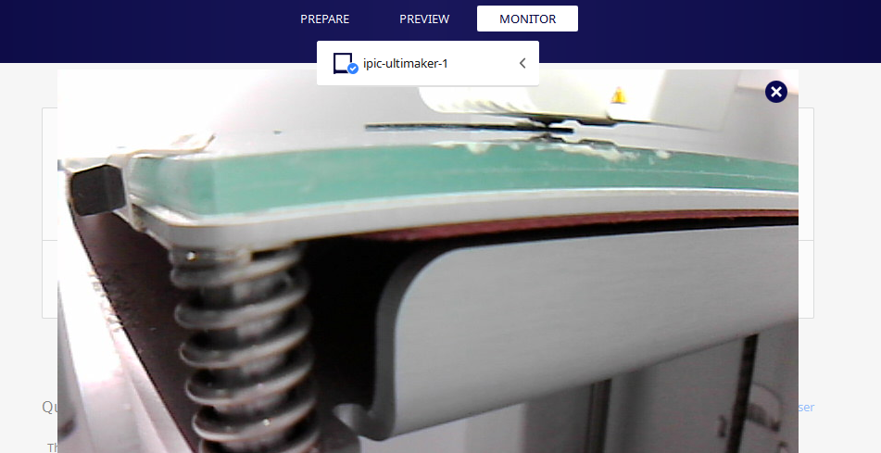
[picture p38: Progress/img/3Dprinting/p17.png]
[](img/3Dprinting/p17.png)

### 18. Monitor tab where you can find the progess

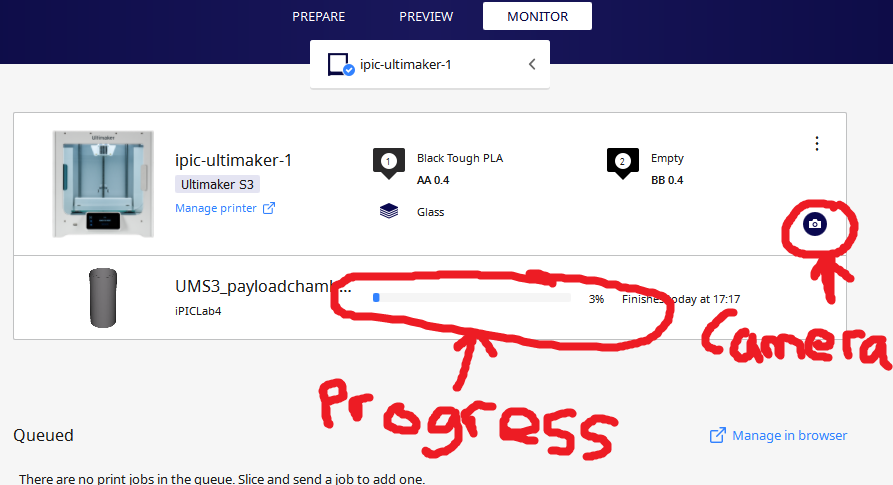
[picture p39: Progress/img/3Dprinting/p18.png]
[](img/3Dprinting/p18.png)

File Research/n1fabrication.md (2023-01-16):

# Design and fabrication of model rocket airframe using 3D printing

## Abstract

In this paper, we describe the method to design and fabricate the airframe of the model rocket. Considering the lack of commercially available model rockets in Kenya, we designed and fabricated a low-cost model rocket using 3D printing. The airframe subsystem comprises a nose cone, body tube, fins, and parachute. For the material of the parachute, we chose nylon considering the lightweight and strength. The aerodynamic stability was confirmed by calculating the static margin using Openrocket software. 
We launched the developed model rocket and confirmed each subsystem worked properly. We believe this model rocket will be used for further development of the flight control system. 3D printing allowed us to iterate over the designs and to make changes effectively. 

## Introduction

### Background information

Nakuja is a team of students from Jomo Kenyatta University of Agriculture and Technology (JKUAT) and Pan African University Institute for Basic Sciences Technology and Innovation (PAUSTI). We are focused on learning as we design, build and launch a rocket into the earth's orbit. The project began in June 2019 with the initial goal to design a rocket using a liquid propellant, which remains our primary goal[1]. The culture at JKUAT emphasizes building tangible engineering solutions to solve the needs of humans. This may sound controversial but JKUAT is leading its way in the best engineering universities in the East Africa Region. With this culture deeply engraved in every human that passes through JKUAT, Dr Aoki decide to make space exploration a reality in Kenya. Model rocketry has been a dream for most engineering students and some end up pursuing aerospace and aeronautical engineering. High powered rocketry began in the mid-1980 with the availability of large motors that were safe. Model rocketry was accepted wholeheartedly when the Nakuja project was launch. For a start, we planned to go up to 50m to test the skills we had acquired while reading. This imposed some constraints on the airframe of the model rocket. We decide to go with a 50mm wide body and a 1-metre long rocket. Since we needed to build and test the rockets almost weekly there was no cheaper way of producing model rockets than 3D printing. Additive manufacturing also referred to as 3D printing is a rapidly growing field that is to radically change the manufacturing landscape. With the advent of even chocolate 3D printers, it is safe to assume a lot of research is going on to help achieve that. As the cost of entry for 3d printing continues to fall, material wastage and energy being minimal, smaller production runs which are often faster and less expensive and easy to recreate and optimize parts we saw it as a suitable candidate for manufacturing. We also had in mind PVC which offered some disadvantages at that moment. Additive manufacturing allows the fabrication of digital design parts using a layer by layer additive process, continually adding material to the base layer as you progress up.

### Introduction 2

This study develops and tests a small solid-propellant rocket utilizing additive manufacturing during design and fabrication. For this, we will be using an F class motor, with passive control to be able to fly up to 50m. We carried a small payload inside. Examples of such rockets are model rockets for education and research [2, 3] and rockets for scientific instruments[4]. We subdivided our rocket into modules that were designed and fabricated independently. This design technique is used in smartphones and also cars, where you can control the product more effectively as modules e.g the apple A-series chip. 

## Method

Product modularization is the process of decomposing a complex system into standardized and more easily manageable subsystems with major characteristics:

1. The subsystems are composed of a high percentage of standard off-the-shelf components
2. The subsystems are easily serviceable and recyclable
3. The subsystem itself or any of its components can be replaced or upgraded by the user at will
4. The modular system offers time or cost savings or another significant benefit to the user, compared with a non-modular system for the same task.

All AM parts are, by definition, one-off parts; complex and straightforward , standardized parts are equally difficult to supply . From this data , it's clear that a modularity-based design process for additively manufactured products requires a wedding of both modularity principles and traditional non-modular design principles.

### Rocket design

In order to demonstrate the additive manufacturing-based approach, we designed a simple small solid-propellant rocket. We were using an F65 motor. The diameter was 40mm and length of 200mm. This motor was designed by the propulsion team at Nakuja. This forms our basis of design. We decided to make a 50mm internal diameter and the motor will be mounted using a motor mount and an engine block. We designed 4 parts namely the nose cone, payload chamber, body tube and tail section. Our initial designs were done in openrocket. Head over to Edit then Preference menu. Configure the atmospheric condition. {Insert image of preferences tab}. Since we will be using additive manufacturing we selected black tough PLA since it was readily available. Move over to the materials tab and add the material you are intending to use if it is not included. {Insert the material image}. The next step is to get the thrust curves from the propulsion team. Get the motor thrust curves from Nakuja Propulsion Team for the N1 motor. Found [here](https://github.com/nakujaproject/N1-motor.git). If you want to use the N1 motors created by the Nakuja Propulsion team, go to general settings then under the user-defined curves add N1-motor\ directory, which we have just cloned, inside there. {Insert motor config image}.
Nose cone configs:

* Parabolic series
* Length 250mm

Parachute

* 1000mm Diameter
* 120 mm length of strings

Shroud lines:

* 6mm 0.25 inch
* 8 lines
* 100mm lenth

Shock cord

* 12mm 0.5 inch
* 100mm length

Body tube:

* Inside diameter 50mm
* Outside diameter 53.6mm
* Length 100mm

Altimeter

* Diamater 50mm
* Length 100mm

Electronics bay

* Inside diameter 48mm
* Outside diameter 50mm
* Length 120mm
* Altimeter block at 5mm from the nose cone

2 Extra tube

* Inside diamter 50mm
* Outside diameter 53.6mm
* Length 150mm
  
2 Launch lugs

* Inside diameter 10mm
* Outside diameter 13.6mm
* Length 30mm

Tail

* Inside diamter 50mm
* Outside diameter 53.6mm
* Length 250mm

Trapezoidal fins

* Thickness 3.6mm

Engine block

* Diamter 50mm
* length 10mm

### Parachute Ejection

This is how we will eject our parachute so that we can be able to recover our rocket after launch. There are many ways to recover the rocket mainly subdivided into pyrotechnics and non-pyrotechnics. I decided to use non-pyrotechnics as it mainly faults tolerant and easier to make.

One mechanism in DetMech was developed to automatically detach a rocket from its parachute line based on the apogee of the rocket. It is designed to assist in recovering rockets stagged by their parachutes. This method utilizes the use of a servo motor to open and close the hatch in order to eject the parachute.

How it works
The mechanism is based on a simple clamp that holds the latch onto the nose cone. At the appropriate time, after maximum height has been reached with a specified delay, the clamp is moved which releases the parachute. By attaching the latch, nose cone and payload chamber to the parachute you will have a better chance of recovering the whole rocket.

The clamp is made up of a micro servo arm which is made of plastics. The latch on the other hand is made up of tough PLA material used in 3D printing the whole rocket. There can be a large lateral force on the clamp during parachute opening. Aerodynamically, it has a low profile.

The bottom plate, payload chamber, which houses the electronics, is attached to the nose cone with screws rather than being glued due to large forces involved. The main parachute line should be fitted with a shock cord to reduce the stress on the clamp.

There is a little groove is to prevent the latch from moving side to side. This mechanism is controlled by the flight computer. This gives the rocket crew a chance t retrieve the rocket easily.

### Recovery mechanism

This is the actual deployment of the recovery mechanism in slowing down the rocket. This also includes opening latches to push out parachutes.

Some examples of the recovery mechanisms are:

1. Parachutes. This is the most effective method of the recovery system.
2. Side deployment. The parachute is ejected on the outside of the rocket using some kind of spring mechanism
3. Inline deployment. The parachute is ejected along the axis of the rocket.
4. Streamer. It is deployed the same as the parachute.
5. Wings, glider. This is commonly used as a passive control.
6. Changing CG, This involves changing the weight of the rocket in order to shift stability.
7. Changing CP, centre of pressure in order to move air surfaces to change the flight's stability.
8. Balloon. A balloon can be inflated from an internally stored pressure chamber in order to increase the rocket's drag.

For the N1 rocket, we choose the parachute system. This is to slow the rocket to an acceptable descent rate to ensure the survival of the avionics. There is usually a backup system e.g deploying to parachutes or using two different methods.

A parachute is basically a flexible device whose function is to produce drag. It slows down the rocket to a decent speed.

Dual deployment means there is a primary and secondary parachute to reduce the impact. The first is generally stronger to overcome large velocities and stabilize the rocket. The second one is attached to the first one via a tow-line and is used to reduce drift away from the launch site.

A shock cord, rubber band, is used as a gravity coupler. This is to store kinetic energy before opening up the parachute.

The main canopy is attached to the towline to provide a soft landing

{Insert images}

Parachute Forces

From the diagram above we can clearly see, according to Newton, the addition of more drag (an adverse force) results in a lower acceleration.

{Insert images}

Newton Second Law

Whether the body decelerates (negative acceleration) or not depends on the velocity and altitude of the parachute deployed.

If the body has a high velocity at parachute ejection, the drag may be greater than the weight.  In this case, the body will decelerate. If the body has a low velocity at parachute ejection, the drag may be lower than the weight.  In this case, the body will accelerate.

Velocity changes so as the drag. At the equilibrium point, the drag is equal to the weight.

If drag starts off lower than weight, acceleration will be positive. This increases velocity and drag. Drag will eventually equal weight and acceleration become zero.

When velocity isn't changing it has reached terminal velocity and it will descend at a constant velocity.

For terminal velocity drag = weight.

The parachute design process needs:

* desired shape
* weight
* drag coefficient
* determine impact velocity
* canopy area

At terminal velocity, the drag should be equal to the weight, 9.8067 N

The drag coefficient itself depends on the Reynolds number Re. For a small enough Reynolds number (of the order of a few thousands or smaller) the dependence is mild and the drag coefficient is approximately constant.

{Insert images}

Area calculation

Hints:

1. Get the atmospheric temperature of where I am testing, [Juja](https://www.accuweather.com/en/ke/juja/828638/hourly-weather-forecast/828638)
2. Calculate the air density of where you are testing, [Juja](https://www.omnicalculator.com/physics/air-density?c=KES&v=P:1013!hPa,Temp:28!C,aaa:1.000000000000000,T:11!C)
3. Check if our area provides the drag equal to the weight, [here](https://www.omnicalculator.com/physics?c=USD&v=Cd:0.7,u:2!ms,rho:1.1661!kgm3,A:6.00702!m2)

### CFD

Now that the designs are established, performance analysis on the rocket designs can begin. In order to guide expectations from the launch experiments and aid in interpreting the results, some preliminary performance knowledge is significant . To estimate these performance characteristics, a digital wind tunnel model was constructed using the Autodesk computational fluid dynamics (CFD). First, the drag coefficients for every of the designs were calculated so as to supply input for preliminary analytical performance analysis. For each of the designs, the coefficient of drag was found at various speeds, from 10 to 100 m/s, and plotted. The fluid tested was air at one atmosphere of pressure, 28 degrees Celsius, and with a medium turbulence factor of 0.05. The cross-sectional areas for every rocket design were identical; the differences in drag were thanks to the varied geometry combinations of fins.
The geometry of each rocket was created using commercial 3-D modelling software and imported into the Autodesk Fusion geometry environment. Within this environment, a fluid domain was modelled around the rocket; the domain was square in cross-section and provided approximately 0.5 m of fluid distance from each surface of the rocket.
Upon geometry and fluid domain definition, the model was meshed using the Autodesk CFD mesh environment. The mesh was set to fine for the entire domain, generating around 1.8 million elements per rocket, 380, 000 of which were in the domain very near the interface between the rocket and fluid.
The centre of mass and centre of pressure for the rocket was found automatically by the software. The airspeed was set within this domain. Convergence tolerance was specified to be 1 × 10−5 with no limit on the allowed number of model iterations.
The model was then analyzed in Autodesk CFD to find the drag coefficients on the rocket bodies. The drag was measured by tracking the force on the rocket body, in the direction of fluid flow, until a steady-state was reached. The average number of iterations to a convergence of 1 × 10−5 was about 650, requiring around 25 min to run for each case.

### FEA

As the drag coefficients were calculated in the previous section, an analytical dynamic analysis can be performed on the rockets in order to predict the flight altitude (apogee). The flight analysis is subjected to the following assumptions:
The air is static (no significant wind); 
The properties of the air remain constant throughout the flight; 
At the top of a time delay following burnout, the rocket motor will stop free-flight motion by ejecting the payload, during this case, an instrument package and recovery system.

## Results

The main purpose of this study was to develop, design, and test an airframe design supported feature modularization into complex parts, rather than part modularization into subassemblies. The rocket airframes utilized in this study were inbuilt three parts; the booster, the payload, and therefore the ogive . In a real aircraft, like a test rocket or missile, the booster section would contain all the propulsion components, the payload section would contain the warhead or instruments, and the nose cone would carry the guidance system and computer. Based on the necessity of the mission and therefore the sizes of the AM equipment available, the amount and scope of the complex parts are often adjusted.
The rockets used in this study were deliberately manufactured out of polylactic acid (PLA) because it is biodegradable and fully recyclable; if any rockets were lost, the pollution to the environment would be minimal. Rockets made up of the quality ABS would be significantly lighter but aren't in the least environmentally friendly or as easily recyclable.

## References

[1]. https://nakujaproject.com/about.html
[2]. Sneider, C.; Kurlich, K.; Pulos, S.; Friedman, A. Learning to control variables with model rockets: A neo-piagetian study of learning in field settings. Sci. Educ. 1984, 68, 465–486. [Google Scholar](https://scholar.google.com/scholar_lookup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,+C.&author=Kurlich,+K.&author=Pulos,+S.&author=Friedman,+A.&publication_year=1984&journal=Sci.+Educ.&volume=68&pages=465%E2%80%93486&doi=10.1002/sce.3730680410) [CrossRef](https://dx.doi.org/10.1002/sce.3730680410)
[3]. Stein, G. H. Forty Years of Model Rocketry: A Safety Report; Publication of the National Association of Rocketry: Marion, IA, USA, 1997; Available online: [http://www.nar.org/pdf/40years.pdf](http://www.nar.org/pdf/40years.pdf) (accessed on 18 January 2017)
[4]. Wilkening, D. Airborne Boost-Phase Ballistic Missile Defense. Sci. Glob. Secur. 2004, 12, 1–67. [Google Scholar](https://scholar.google.com/scholar_lookup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,+D.&publication_year=2004&journal=Sci.+Glob.+Secur.&volume=12&pages=1%E2%80%9367&doi=10.1080/08929880490464649) [CrossRef](https://dx.doi.org/10.1080/08929880490464649)
[5]. https://www.mdpi.com/2226-4310/4/2/17/htm
[6]. http://vestnikmai.ru/eng/publications.php?ID=116216&mobile=Y

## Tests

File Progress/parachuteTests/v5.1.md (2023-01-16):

# Version 1.1

## Introduction

On this nose cone design we inserted a pin on the top part need the nose. This is to hold the nose part while the servo pushes it in from the bottom. We then added the spring mechanism to the base part this was to create an outward force to push the parachute out. This was done while maintaining the previous specs. The design can be found [here](https://github.com/nakujaproject/airframev1/tree/8eca6001235c1c59b9d69e9f7931666770087936)

### Some images

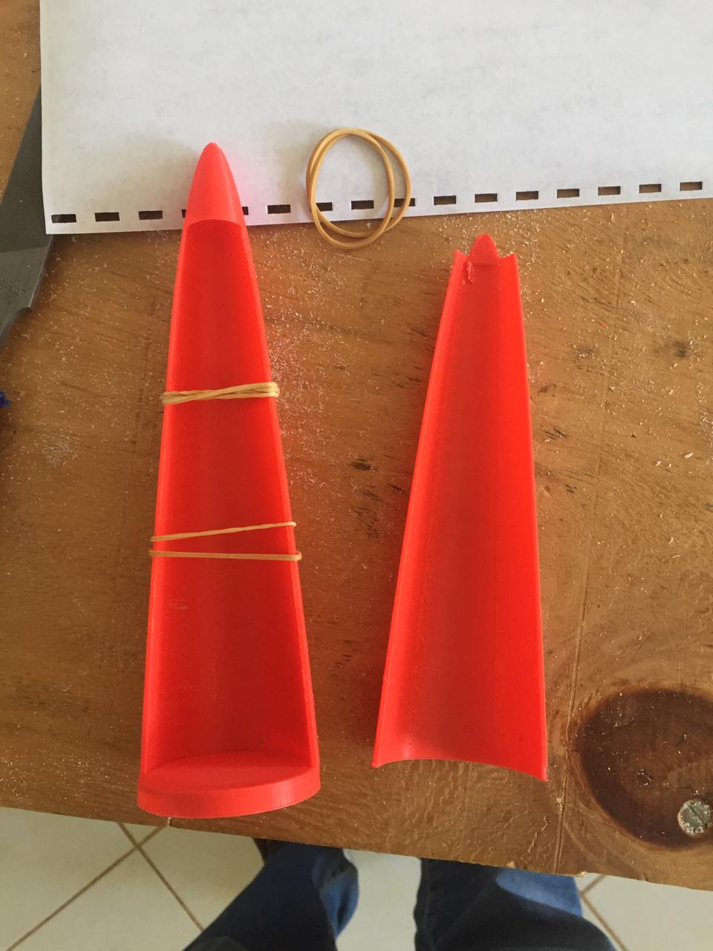
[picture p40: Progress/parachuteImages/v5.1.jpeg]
Nose cone image v5.1


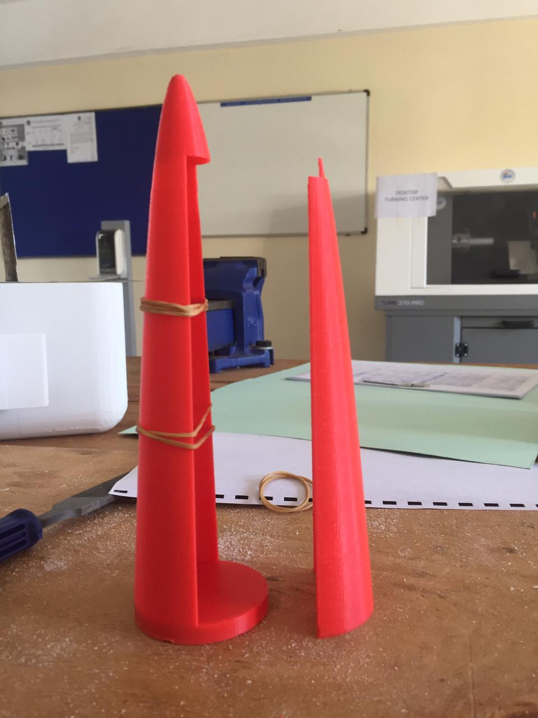
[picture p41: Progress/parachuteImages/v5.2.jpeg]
Nose cone image v5.2


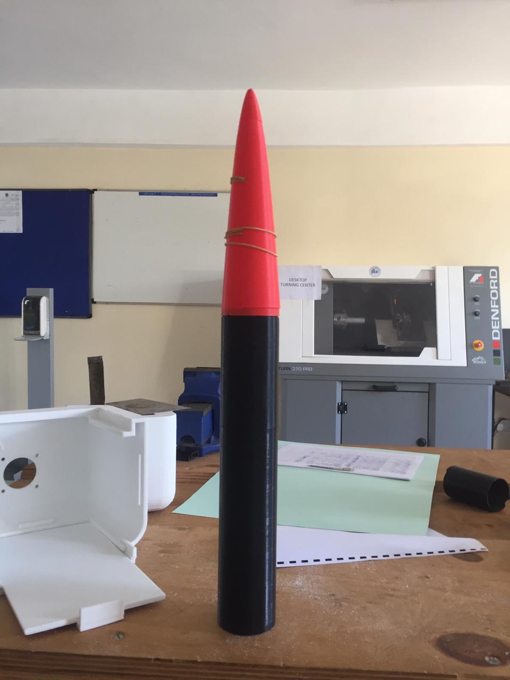
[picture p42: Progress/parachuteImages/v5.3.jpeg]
Nose cone image v5.3


## Problem

No problem so far awaiting testing

## Modifications

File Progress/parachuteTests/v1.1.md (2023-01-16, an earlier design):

# Version 1.1

## Introduction

This was pur first nose cone design for the rocket. We didn't have any prior know how on how the parachute ejection mechanism would work. The design files can be found [here](https://github.com/nakujaproject/airframev1/blob/e236fa8ae708f634feae82047ced389b07deac66/Design/nose-basepart1.stl)

### Some images

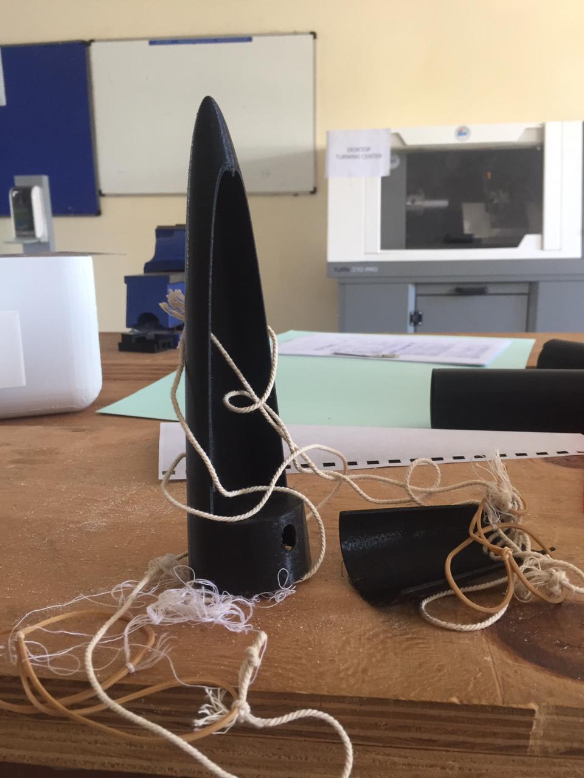
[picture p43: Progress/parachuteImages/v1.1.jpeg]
Nose cone image v1.1


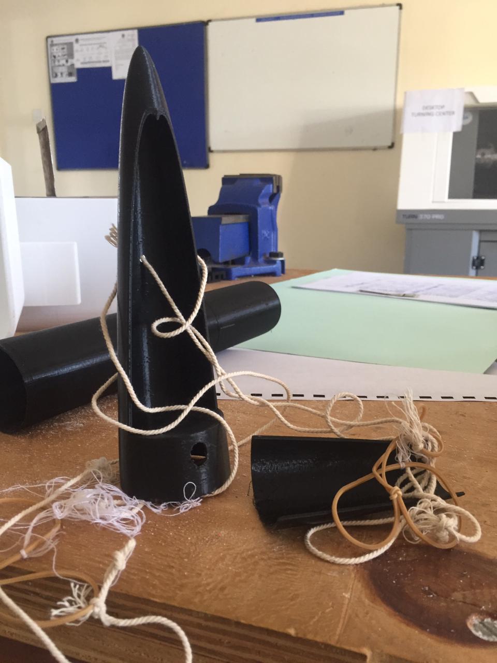
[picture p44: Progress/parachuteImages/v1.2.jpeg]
Nose cone image v1.2


## Problem

The parachute was not able to open up since the walls of the base part of the nose cone constrained it from ejecting.

## Modifications

We tried and make the opposite. So that the base part that joins with the rocket has less material while the cover covers all of it.

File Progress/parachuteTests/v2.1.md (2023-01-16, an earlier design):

# Version 2

## Introduction

This was our second nose cone design for the rocket. We tried and make the opposite. So that the base part that joins with the rocket has less material while the cover covers all of it. The servo mechanism remained the same to be able to hold the cover before opening it up. The design can be found [here](https://github.com/nakujaproject/airframev1/tree/cf36e4de9e948d365fbf606aeacae3a5e0503ae5)

### Some images

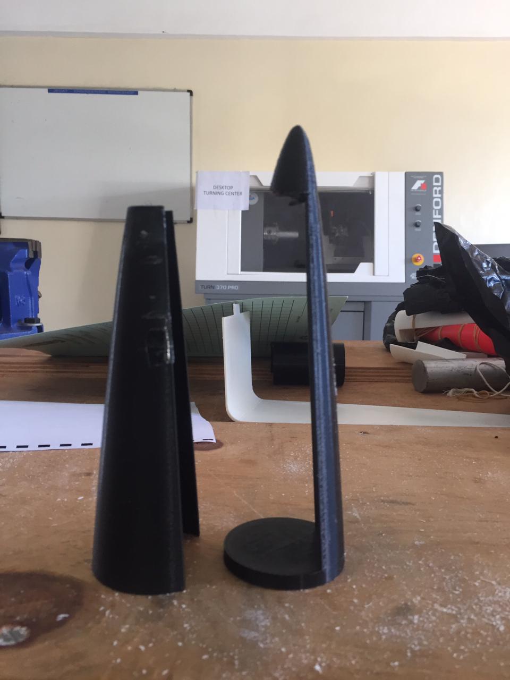
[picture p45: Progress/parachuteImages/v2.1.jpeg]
Nose cone image v2.1


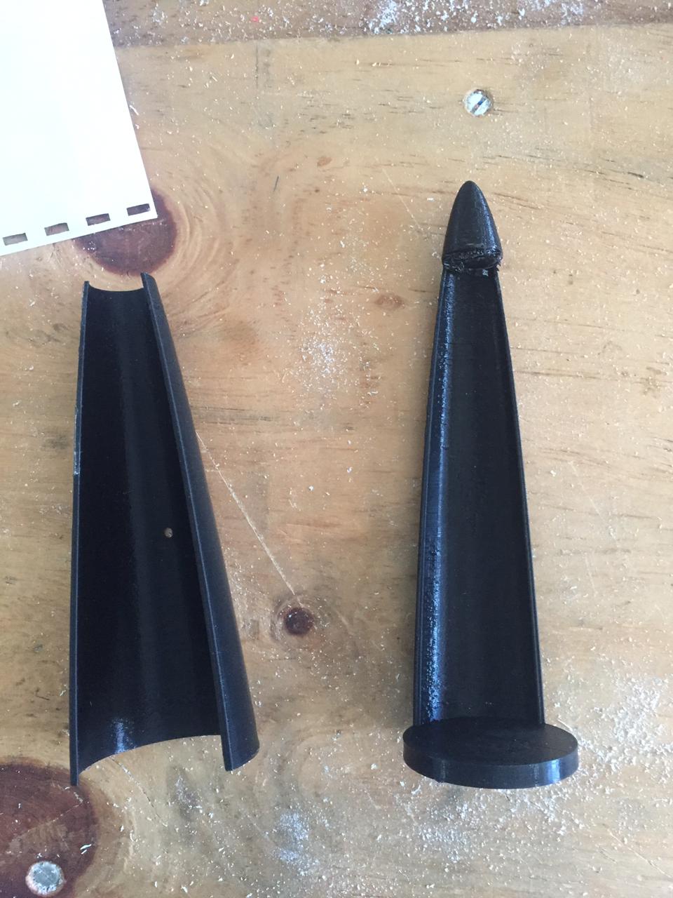
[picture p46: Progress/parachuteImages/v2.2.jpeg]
Nose cone image v2.2


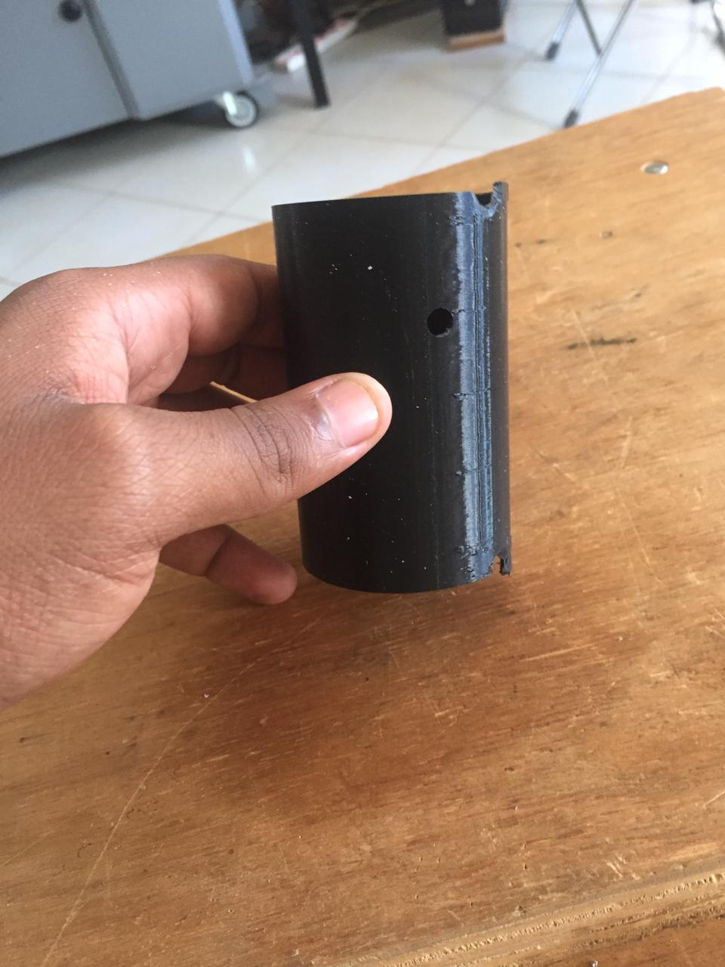
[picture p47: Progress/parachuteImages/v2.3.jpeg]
Nose cone image v2.3


## Problem

The servo arm was able to release the cover of the nose cone outside but the parachute still had trouble in deploying. Parachute was holding on to the cover this time instead of releasing.

## Modifications

We tried and made the cover to have 60% and the base have 40% of the total material coverage so that the parachute could have and easier time releasing. We also added the servo mechanism inside, so that it could push out the top part.

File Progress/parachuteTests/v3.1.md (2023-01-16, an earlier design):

# Version 3.1

## Introduction

This was our third nose cone design for the rocket. We tried and redesign the latch mechanism so that the servo arm could push the cover outside rather that the servo arm holding the cover inside before launch. The design can be found [here](https://github.com/nakujaproject/airframev1/tree/cf36e4de9e948d365fbf606aeacae3a5e0503ae5)

### Some images

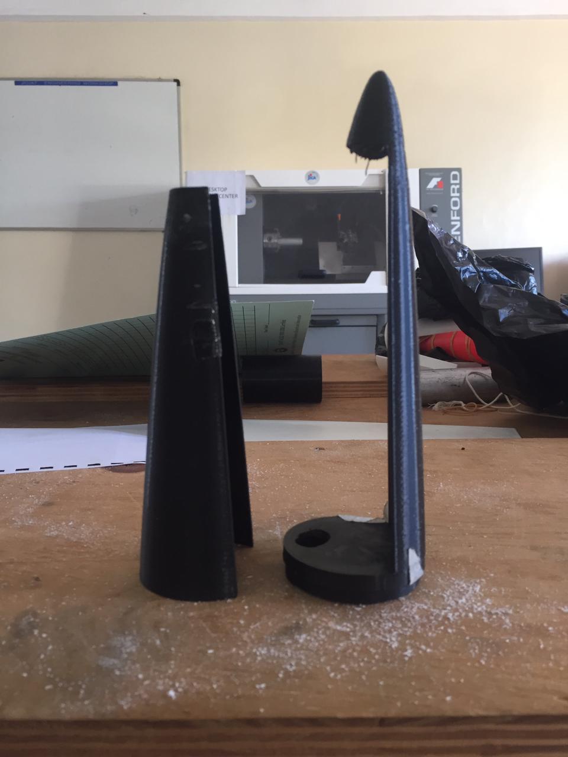
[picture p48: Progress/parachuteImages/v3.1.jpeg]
Nose cone image v3.1


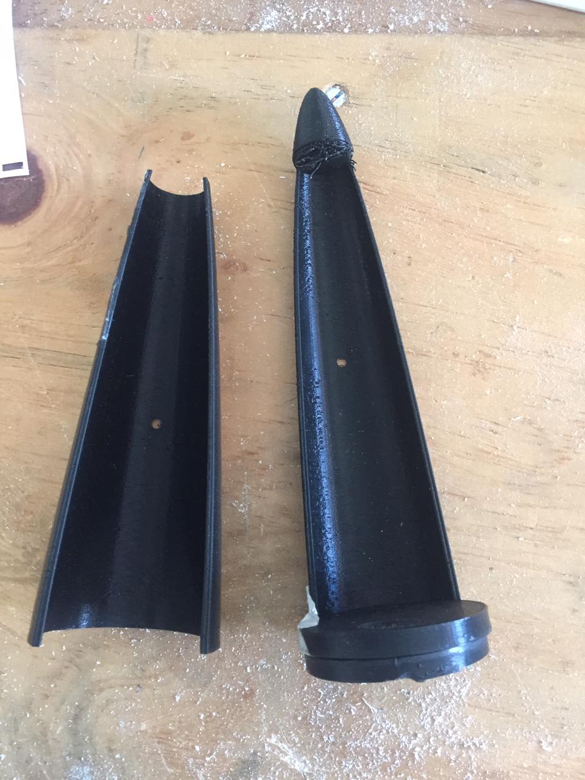
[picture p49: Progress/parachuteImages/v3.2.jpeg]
Nose cone image v3.2


Nose cone test v4.1

<!-- blank line -->
<figure class="video_container">
  <video controls="true" allowfullscreen="true">
    <source src="../parachuteImages/v3.1.mp4" type="video/mp4"></source>
  </video>
</figure>
<!-- blank line -->

## Problem

The servo arm was able to push the cover of the nose cone outside but the parachute still had trouble in deploying

## Modifications

We tried and make the opposite. So that the base part that joins with the rocket has less material while the cover covers all of it.

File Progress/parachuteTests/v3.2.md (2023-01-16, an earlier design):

# Version 3.2

## Introduction

On this nose cone design we tried and have it half-and-half so that the base part could cover half and also the cover to cover half. This was in order to make sure the parachute doesn't attach itself to the base part. We also added our first electronics chamber for the rocket. This is the chamber that houses the electronics bay which holds the electronic components. The servo mechanism was to shift from the nose to the electronics chamber. The design can be found [here](https://github.com/nakujaproject/airframev1/blob/8eca6001235c1c59b9d69e9f7931666770087936/Design/nose-basepart1.stl)

### Some images

Nose cone image v3.2

## Problem

The parachute maintained to attach itself on the top part rather than the base part. This make the ejection difficult since the parachute couldn't eject freely. When we were drilling we started off with a larger drill bit to drill the whole hole at once. The forces on the cutting edge corner were to high hence the electronics chamber weakened on the additive layers of 3D printing.

## Modifications

Trying to add spring mechanisms to the top part which covers the base part. This is to create an outward force which pushed the parachute out. We tried the next test starting of with smaller drill bits and gradually increasing the drill bit by a deviation of 1mm. We succeed in drilling through and mounting the servo motor.

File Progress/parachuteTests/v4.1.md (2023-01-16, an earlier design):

# Version 1.1

## Introduction

On this nose cone design we tried and have to change the dimensions rather than having it half-and-half so that the base part could cover half and also the cover to cover half, we had the base part to be at 70% and the top part at 30% of the coverage. We then added the spring mechanism to the base part this was to create an outward force to push the parachute out. The design can be found [here](https://github.com/nakujaproject/airframev1/tree/601282b1a38ceb6b29486d730ce19b3bf3055e32)

### Some images

Nose cone image v4.1

Nose cone test v4.1

<!-- blank line -->
<figure class="video_container">
  <video controls="true" allowfullscreen="true">
    <source src="../parachuteImages/v4.1.mp4" type="video/mp4"></source>
  </video>
</figure>
<!-- blank line -->

## Problem

We didn't find a mechanism to hold the top part to the base part. So the cover was not holding the parachute in and could fly off any time possible.

## Modifications

We inserted a pin on the top part need the nose. This is to hold the nose part while the servo pushes it in from the bottom.

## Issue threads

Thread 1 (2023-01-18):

Review on the type of material to be used

Ci-Daniels, 2023-01-18:

rodneyosodo, 2023-01-19:
I'd suggest we design for both Aluminium and Fibreglass i.e we have two versions

rodneyosodo, 2023-01-19:
@shohei were the new CNC machines installed for better fabrication?

shohei, 2023-01-19:
@rodneyosodo The new desktop CNC machine (Kitmill AST 200) may not suitable for PCB milling as it targets light metal cutting.

shohei, 2023-01-19:
@rodneyosodo A CNC for woodworking (Shopbot PRS alpha) is being installed at carpentry workshop. The arrival of the CNC lathe is delayed and it will arrive in April. A water jet cutter will be also installed soon.

Closed 2023-02-10.

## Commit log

2023-02-10 Added progress meeting and CAD design files
    [Final assemblyv2 v9.step, N3 Avionics bay.step, N3 Bottom coupler.step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]
2023-02-10 Resolves nakujaproject/airframeN3#14: Research on motor mount design
2023-02-10 Adds reference files for motor mount design
    [Motor Mount Config 2.iam, Motor mount Config 1.iam]
2023-02-10 Replaces .iam files with jpg files within the text
    [Motor Mount Config 2.iam, Motor mount Config 1.iam]
